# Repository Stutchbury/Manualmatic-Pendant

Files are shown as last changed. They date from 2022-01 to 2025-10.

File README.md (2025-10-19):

# The Manualmatic Pendant for LinuxCNC (or any other 4D system)

The Manualmatic Pendant enables you to perform the majority of routine LinuxCNC setup, manual and automatic operations without having to step away to a PC monitor.

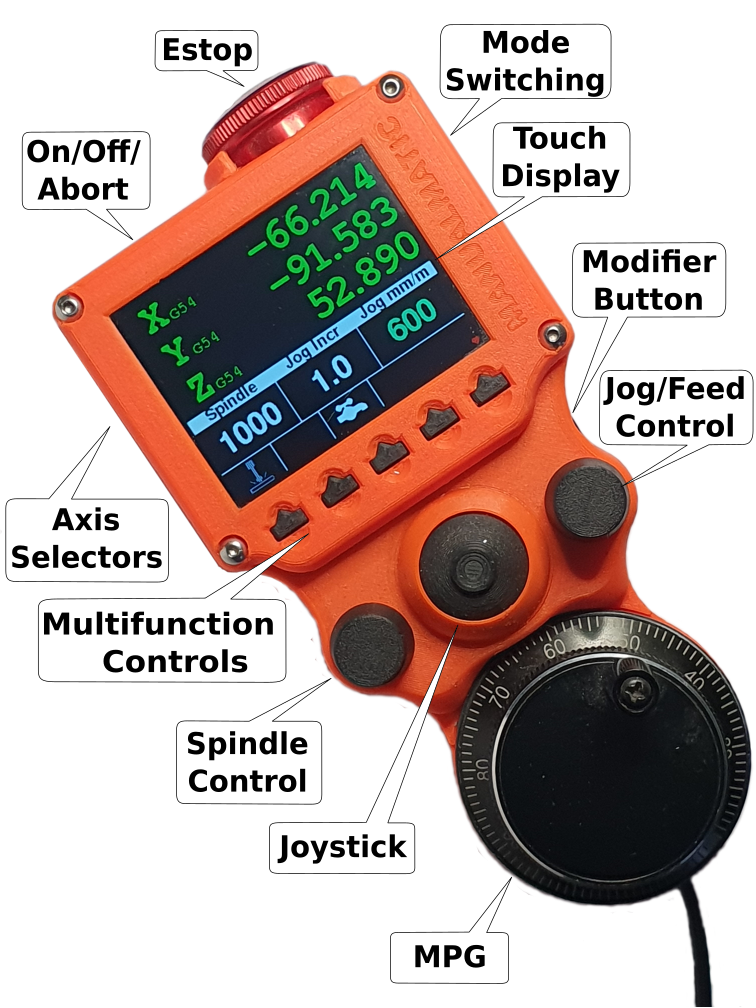
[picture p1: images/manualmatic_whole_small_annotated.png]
Manualmatic Controls Overview


Kicked off [here](https://forum.linuxcnc.org/18-computer/44682-arduino-teensy-python-interface-manualmatic-mpg-pendant) on the LinuxCNC forum and there's my place on [Discord](https://discord.gg/GDcEcWPKKm) for questions or discussion (PMs OK).

> User Guide **See the [User Guide](docs/USER_GUIDE.md) for the many features and functionality provided by the Manualmatic Pendant**

The currently released code implements almost all the functionality for both manual and auto control but don't take my word for it, here's a comment from das_machinist on [Discord](https://discord.gg/GDcEcWPKKm):

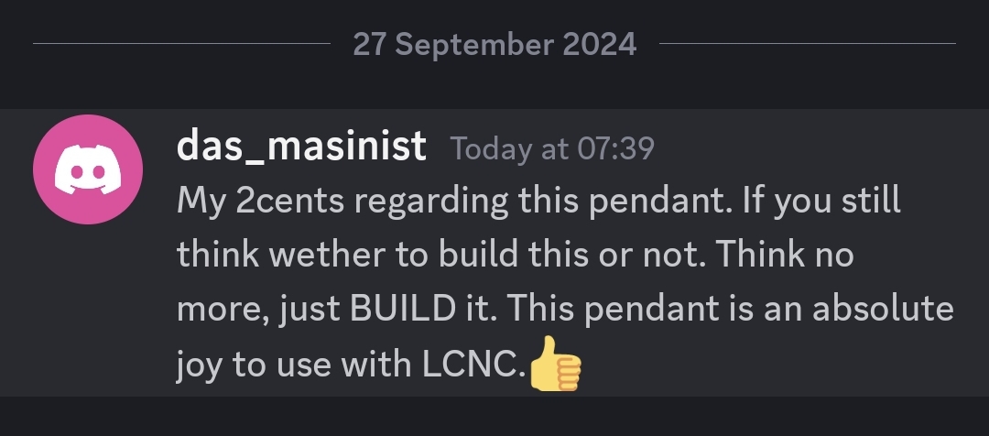
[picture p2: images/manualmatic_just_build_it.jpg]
Manualmatic Just Build It


Auto mode screen (uses the [DisplayUtils](https://github.com/Stutchbury/DisplayUtils) library):
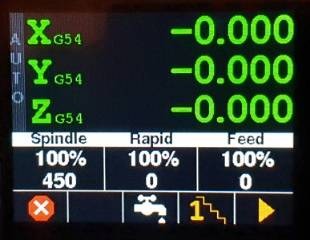
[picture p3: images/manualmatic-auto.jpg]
auto screen


Setting offsets (uses the [TouckKeypad](https://github.com/Stutchbury/TouchKeypad) library):
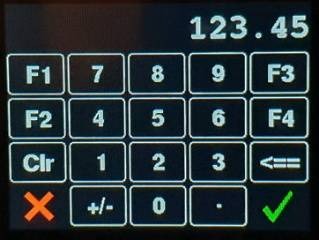
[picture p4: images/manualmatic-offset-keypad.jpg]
offset screen


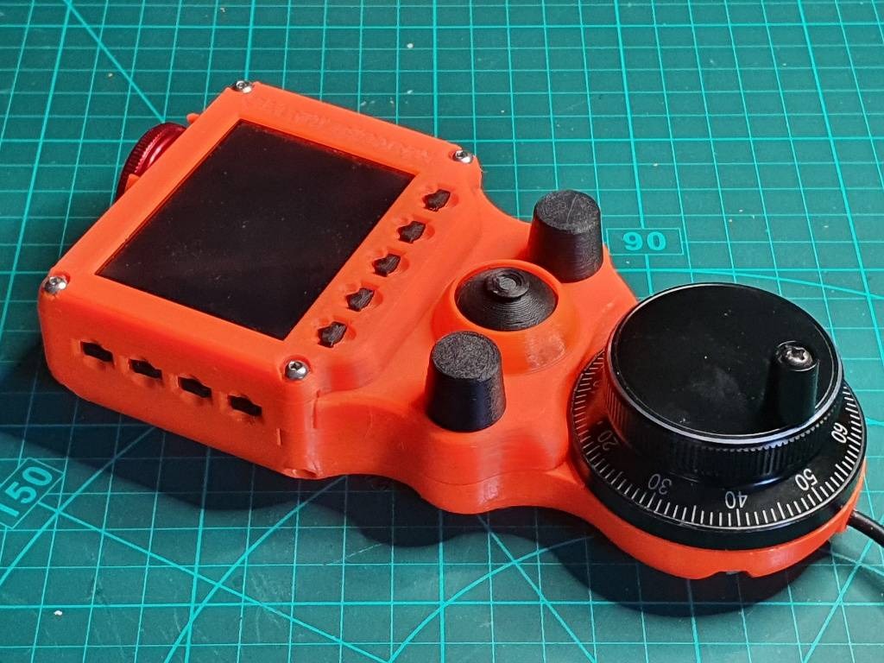
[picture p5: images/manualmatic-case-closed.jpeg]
manualmatic case
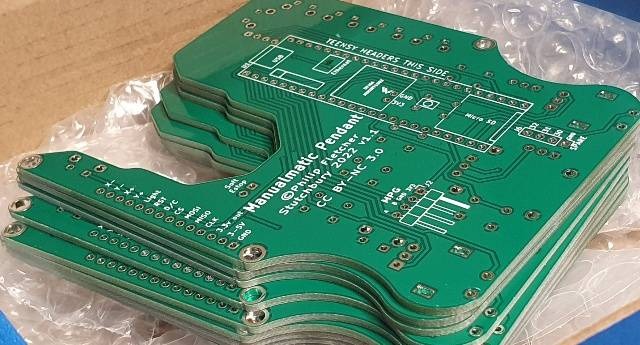
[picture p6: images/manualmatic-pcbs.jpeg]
manualmatic PCBs
There is now a complete 3D printable case  and a PCB  - contact me for details (email in my bio).

The pendant software has now been migrated to PlatformIO - using [Teensyduino](https://www.pjrc.com/teensy/td_download.html) via the Arduino IDE did end up too knarly.

Communication beween the [Teensy 4.1](https://www.pjrc.com/store/teensy41.html) and the [LinuxCNC Python Interface](https://www.linuxcnc.org/docs/html/config/python-interface.html) is over USB using a very simple protocol.

While the pendant prioritises working with LinuxCNC, in principle it is a fairly agnostic UI to control anything that you'd like to move in 4D that can read from & write to the serial port over USB.

## Getting Started

This was always intended to be "Almost Plug'n'Play"&trade; but does require the PlatformIO to upload to the Teensy and two files copied to your LinuxCNC config directory.

- Clone or download this repository and extract somewhere convenient (not usually on your LinuxCNC machine).

### PlatformIO Install

- Follow the install instructions here: https://platformio.org/platformio-ide

- Required libraries will be automatically downloaded based on the ```platformio.ini``` file.

- There are two folders of interest: 
  - The main codebase for the pendant: ```Software/PlatformIO/pendant/ManualmaticPendant``` or
  - A wiring check 'sketch': ```Software/PlatformIO/pendant/ManualmaticWiringCheck```

Open either of these folders and PlatformIO will allow you to compile and upload.

### LinuxCNC Install

- Copy both ```Manualmatic.py``` (the class def) and ```manualmatic``` (the component, lowercase, no file extension) to your LinuxCNC config directory.
- Add the following line to custom.hal (replace ```gmoccapy.ini``` with your ini file name):    
```loadusr -W ./manualmatic gmoccapy.ini```
- Change the ```manualmatic``` file to executable. e.g. ```chmod +x manualmatic``` 
- Plug your manualmatic pendant into a USB port - make sure appears as ```/dev/ttyACM0```
- Start LinuxCNC, preferably from the command line (to see any errors).

Note: LinuxCNC >= v2.9 now uses python3 with no default to 'python', so the ```manualmatic``` component file and the ```mock_cnc_machine.py``` file have been updated to use python3.

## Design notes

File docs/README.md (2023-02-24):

# Documentation

This folder will contain various documents relating to the build and use of the Manualmatic pendant.

The PCB:
- [Bill of Materials](BOM.md)
- [Soldering order of operations](SOLDERING.md)

3D Printable Case:
- [Printing the Case](../Hardware/case/v1.1/README.md)

Software
- [LinuxCNC Install](LINUXCNC_INSTALL.md)

User Guide
- [This](pendant_user_guide.pdf) is currently more an early development aid rather than a user guide as it describes the functions of each control on the Manualmatic rather than describing how to perform tasks. Rewrite is required...

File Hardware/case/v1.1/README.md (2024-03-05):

# Manualmatic Pendant Case v1.1

Designed around the v1.1 PCB to be 3D printed. Tolerances are built in but you may need to tune your slicer settings to get an accurate fit.

## Base
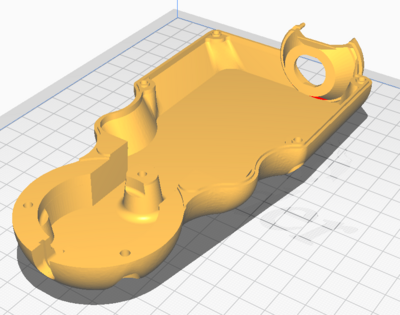
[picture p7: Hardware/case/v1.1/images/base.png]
base


Print 'as is' - will require supports for the MPG and display holes. I also used support for the e-stop shroud but this may not be essential.

## Encoder Panel
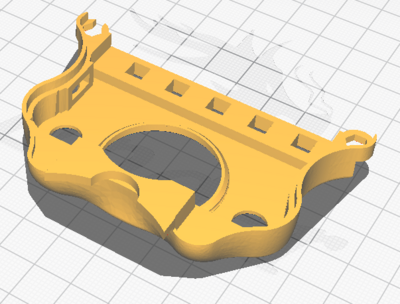
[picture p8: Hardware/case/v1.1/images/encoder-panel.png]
encoder panel


Flip this over to print. Will require supports for the display holes/lugs and the lip that will end up under the MPG. I also generated support for the modifier button hole.

## Left/Right Side Button Panels
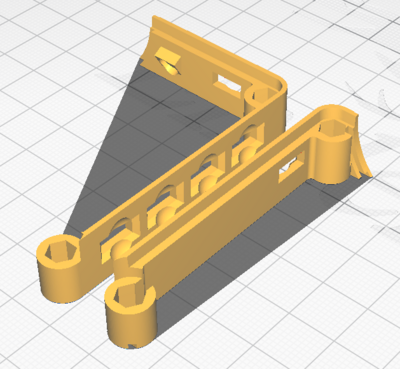
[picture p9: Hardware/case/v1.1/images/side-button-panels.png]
left/right side button panels


Flip over to print - bed adhesion is critical as these have a tendency to warp with PETG, so print in the centre of the bed and, if possible, with an enclosure.
Support is not necessarily required but I generated it for the button holes.
Ensure the top grooves are clear before assembly (test fit with the display bezel).

## Display Bezel
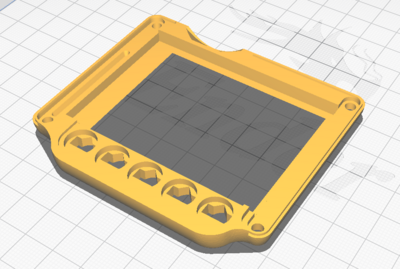
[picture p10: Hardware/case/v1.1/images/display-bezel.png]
display bezel


Flip over to print. Support is required only for the corner hole counterbores. 

## Cable Wedge x2

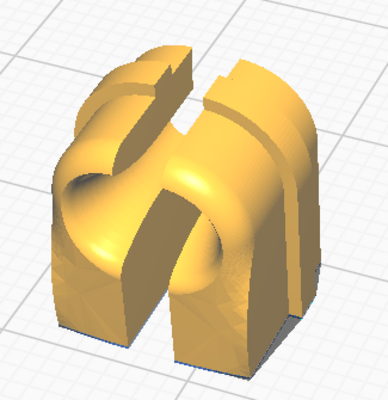
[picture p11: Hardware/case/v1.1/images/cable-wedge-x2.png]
cable wedge


Mirror one part and print both standing on the (only) flat face. Support is advised for the hole.

These should slide fairly easily into the base (ie, don't spring the gap open or you won't get the MPG studs in). Before putting it all together, make sure your cable fits through the hole with the two faces just about touching - to adjust, fit the parts in the base and ream out with a drill bit or needle file.

## Joystick Dome
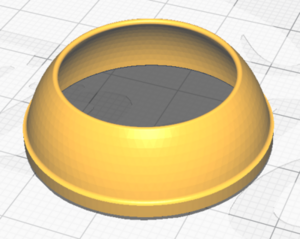
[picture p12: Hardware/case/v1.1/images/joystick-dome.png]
joystick dome


Print 'as is'. Does not require support. Push fit into the top of the encoder panel.

## Joystick Button
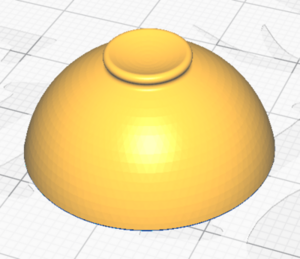
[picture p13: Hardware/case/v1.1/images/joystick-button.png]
joystick button


Print 'as is' - requires support but remove very carefully!

Currently this is an 'inside' button - may redesign as an 'outside' button (ie dome underneath).

## Side Buttons x7
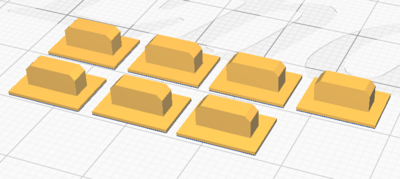
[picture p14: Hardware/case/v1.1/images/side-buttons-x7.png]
side buttons


Print as is. These can be taped to the case (inside) before assembly but don't overlap the rebate.

## Row Buttons x5
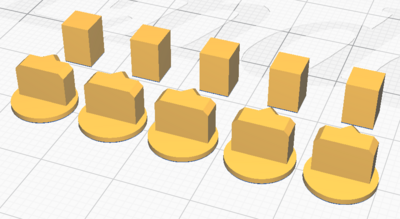
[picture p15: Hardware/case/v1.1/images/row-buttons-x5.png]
row buttons


Print as is - each button is in two parts. The top part can be taped into the display bezel before assembly (there's a little relief for the tape).

## Encoder Knobs x2

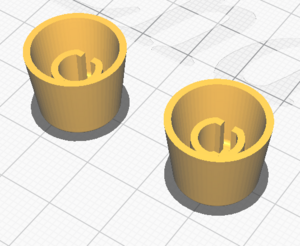
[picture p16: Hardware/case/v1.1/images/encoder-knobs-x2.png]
encoder knobs


Print as is, no support required.

## MPG Spanner

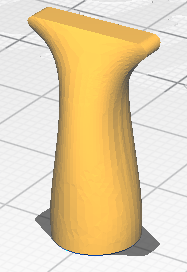
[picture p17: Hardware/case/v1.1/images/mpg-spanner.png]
mpg spanner


Print 'as is', I do not advise using support. 

Use this to hold & tighten the nuts for the MPG.

## Cradle

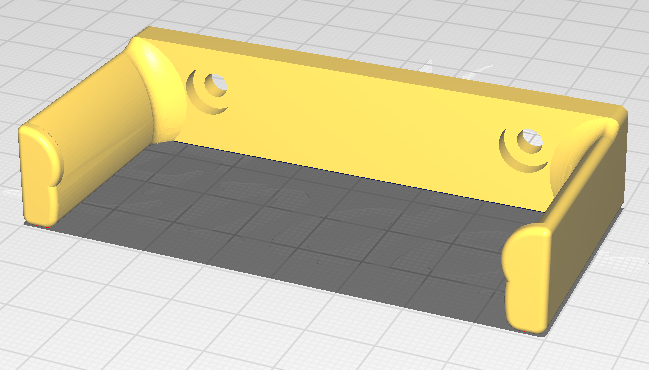
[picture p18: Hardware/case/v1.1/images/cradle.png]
cradle


Print 'as is', no support required.

I used 5 walls to ensure line continuity from fixing holes to support legs.

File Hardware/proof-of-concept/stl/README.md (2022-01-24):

# Proof of concept 3D prints

This is a 'cradle' and 'bridge'to hold the Teensy 4.1, touch screen, buttons and rotary encoders/MPG.

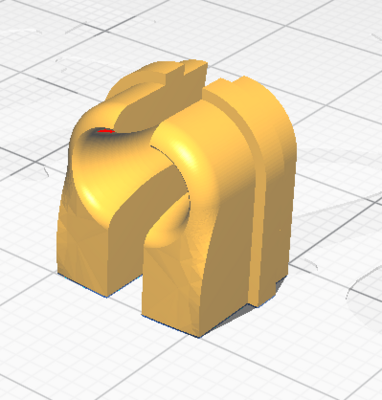
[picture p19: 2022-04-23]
Hardware/case/v1.1/images/cable-wedge.png

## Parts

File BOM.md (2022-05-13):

# Bill of Materials

These are the components I have chosen to use for the Manualmatic when using the PCB.

| Item | Ref	| Qty	| Value | Datasheet |  Manufacturer |
| ---- | ---- | --- | ----- | --- | --- |
|MPG  | U1 |	1	| Teensy4.1| https://www.pjrc.com/store/teensy41.html | Teensy |
|MPG | J1 |	1	| Adafruit-1770-2.8-TFT-Touch	 |	https://www.adafruit.com/product/1770	| Adafruit |
|MPG  | S12 S13 | 2	| PEC11R-4115F-S0018	|	https://www.mouser.co.uk/datasheet/2/54/PEC11R-777457.pdf	| Bourns |
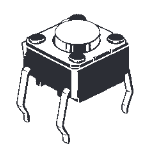
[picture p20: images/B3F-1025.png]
| | S1 S2 S3 S4 S5 |	5	| B3F-1025 |	https://www.mouser.co.uk/datasheet/2/307/en-b3f-13826.pdf	| Omron |
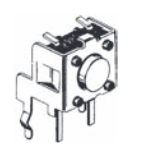
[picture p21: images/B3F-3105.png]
| | S6 S7 S8 S9 S10 S11 S14 | 7	| B3F-3105| https://www.mouser.co.uk/datasheet/2/307/en-b3f-13826.pdf |		Omron |
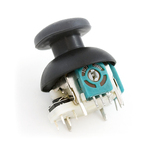
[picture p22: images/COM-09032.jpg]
|  | U2 |	1	|COM-09032	| https://www.sparkfun.com/products/9032	| SparkFun Electronics |
|MPG | J2 | 1 | Right angle male header for MPG| | Generic|

Unless you're brave enough to solder both the Teensy and the Adafruit display to the PCB (I'm not and the case *is not* designed for direct soldering), you'll need 48 female headers for the Teensy and 14 female headers for the display.

I bought these as 4 x 12 pins and 2 x 7 pins as this was significantly cheaper than contiguous blocks. You may need to lightly file adjacent edges so they don't bow the board when soldered in.

You'll also need a 60mm Manual Pulse Generator (ebay ones seem to work just fine, unlike the two encoder buttons), a 16mm Estop button and a tight/compact right angle micro-USB cable (2-3m) - preferably in the orientation shown below.

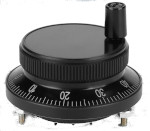
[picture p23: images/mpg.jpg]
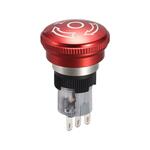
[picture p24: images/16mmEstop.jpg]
estop
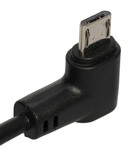
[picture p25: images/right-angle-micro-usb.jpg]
micro USB
   

J3 (2 pin, soft estop), J3, J4 & J5 (3 & 4 pin spare breakouts) are optional right angle male headers.

**Notes:**

1. I recommend sourcing the two encoder buttons from a known supplier unless you are sure of their provenance - I have had two 'ebay specials' fail which have effectively wasted the PCBs. The specified encoders also have a short shaft to work with the case.
2. The 5 push buttons and 7 right angle buttons are of a specific detent force (orange button) and closely match the detent force of the two encoders and the joystick, maximising the consistency of 'feel'. Ebay ones are of very variable detent strength - often very low.
3. The joystick PCB footprint will only fit the Sparkfun Deluxe COM-09032 joystick. The Xbox replacements have a different footprint (and the ebay ones have 'interesting' resistance characteristics).
4. If you are using the 3D printed case (recomended, it's a work of art ;-)), you'll need 4 x 11mm brass stand-offs and 8 x 8-10mm M3 dome/button head screws.
5. We are using the Adafruit display in SPI mode, so you will need to bridge the pads on the back of the board as per: https://learn.adafruit.com/adafruit-2-8-and-3-2-color-tft-touchscreen-breakout-v2/spi-wiring-and-test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

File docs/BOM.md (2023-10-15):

# Bill of Materials

These are the components I have chosen to use for the Manualmatic when using the PCB.

|Num| Item | Ref	| Qty	| Value | Datasheet/Notes |  Manufacturer |
|--| ---- | ---- | --- | ----- | --- | --- |
|1|Teensy 4.1  | U1 |	1	| Teensy4.1| https://www.pjrc.com/store/teensy41.html | Teensy |
|2|Adafruit Display | J1 |	1	| Adafruit-1770-2.8-TFT-Touch	 |	https://www.adafruit.com/product/1770	| Adafruit |
|3|Encoder button  | S12 S13 | 2	| PEC11R-4115F-S0018	|	https://www.mouser.co.uk/datasheet/2/54/PEC11R-777457.pdf	| Bourns |
|4|push button | S1 S2 S3 S4 S5 |	5	| B3F-1025 |	https://www.mouser.co.uk/datasheet/2/307/en-b3f-13826.pdf	| Omron |
|5|right angle push button | S6 S7 S8 S9 S10 S11 S14 | 7	| B3F-3105| https://www.mouser.co.uk/datasheet/2/307/en-b3f-13826.pdf |		Omron |
|6|Joystick  | U2 |	1	|COM-09032	| https://www.sparkfun.com/products/9032	| SparkFun Electronics |
|7|MPG right angle header | J2 | 1 | 4 pin right angle male header| For MPG | Generic|
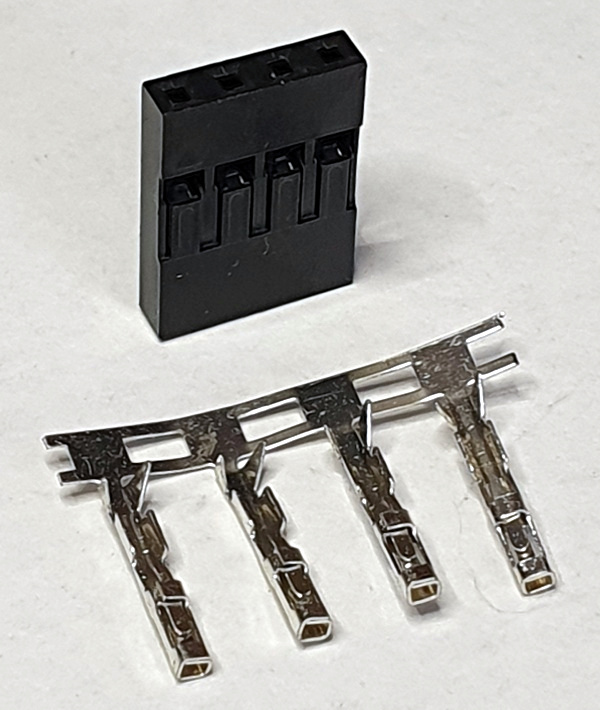
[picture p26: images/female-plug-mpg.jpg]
MPG female plug
|8| | n/a  | 1 | 4 pin female plug| For MPG | Generic|
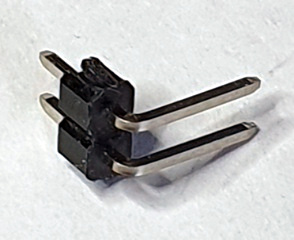
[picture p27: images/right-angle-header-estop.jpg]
Estop right angle header
|9| | J3 | 1 | 2 pin right angle male header | For Estop button | Generic|
|10|Estop female plug | n/a  | 1 | 2 pin female plug| For Estop button | Generic|
|11|Teensy female headers | U1 | 4 x 12pin | Female headers | To plug Teensy into PCB. <br/>8.5mm high, excluding pins | Generic|
|12|Display female headers | J1 | 2 x 7pin| Female headers | To plug in display into PCB. <br/> 8.5mm high, excluding pins | Generic|
|13|MPG | n/a | 1 | 60mm Manual Pulse Generator | ebay ones seem to work just fine, unlike the encoder buttons. Some may have 6 connections but you can ignore A- & B-.| Generic|
|14|Estop | n/a | 1 | 16mm Estop button | Example: https://www.ebay.co.uk/itm/184899597984 | Generic|
|15|USB Cable | n/a | 1| 2-3m tight/compact right angle micro-USB cable | Example: https://www.ebay.co.uk/itm/194756552182?var=494734226747 | Generic|
|16|PCB | n/a | 1 | Custom PCB| Contact me (email address on my profile)  | Stutchbury|
|17|Stand-offs | n/a | 4 | 11mm stand-offs & screws| | Generic |

Unless you're brave enough to solder both the Teensy and the Adafruit display to the PCB (I'm not and the case *is not* designed for direct soldering), you'll need 48 female headers for the Teensy (item 11) and 14 female headers for the display (item 12).

I bought these as 4 x 12 pins and 2 x 7 pins as this was significantly cheaper than contiguous blocks. You may need to lightly file adjacent edges so they don't bow the board when soldered in.

Items 7-10 above can be omitted if you solder the MPG & Estop wires directly to the PCB.

J4 & J5 (3 & 4 pin spare breakouts) are optional right angle male headers.

**Notes:**

1. I recommend sourcing the two encoder buttons from a known supplier unless you are sure of their provenance - I have had two 'ebay specials' fail which have effectively wasted the PCBs. The specified encoders also have a short shaft to work with the case.
2. The 5 push buttons and 7 right angle buttons are of a specific detent force (orange button) and closely match the detent force of the two encoders and the joystick, maximising the consistency of 'feel'. Ebay ones are of very variable detent strength - often very low.
3. The joystick PCB footprint will only fit the Sparkfun Deluxe COM-09032 joystick. The Xbox replacements have a different footprint (and the ebay ones have 'interesting' resistance characteristics).
4. If you are using the 3D printed case (recomended, it's a work of art ;-)), you'll need 4 x 11mm brass stand-offs and 8 x 8-10mm M3 dome/button head screws.
5. We are using the Adafruit display in SPI mode, so you will need to bridge the pads on the back of the board as per: https://learn.adafruit.com/adafruit-2-8-and-3-2-color-tft-touchscreen-breakout-v2/spi-wiring-and-test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

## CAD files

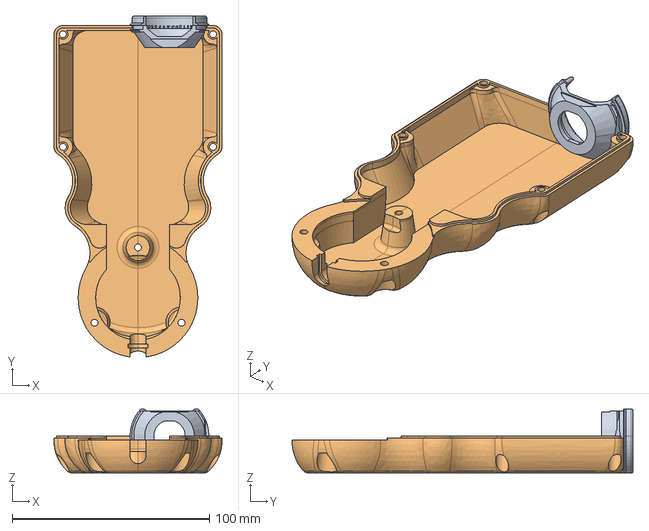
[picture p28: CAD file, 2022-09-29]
Hardware/case/v1.1/step/base-Part.step
85.3 x 173.0 x 32.3 mm

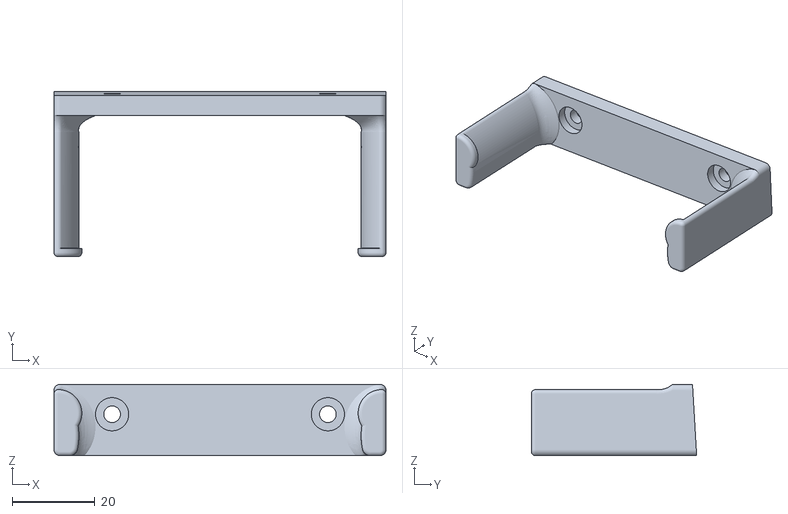
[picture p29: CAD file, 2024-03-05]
Hardware/case/v1.1/stl/cradle.stl
80.0 x 39.8 x 17.2

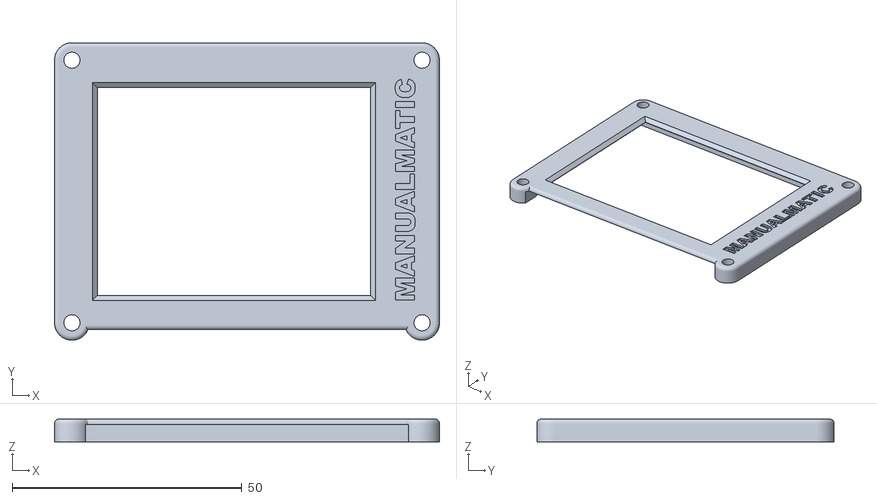
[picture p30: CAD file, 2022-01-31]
Hardware/proof-of-concept/stl/bezel-Part.stl
83.8 x 64.7 x 5.00

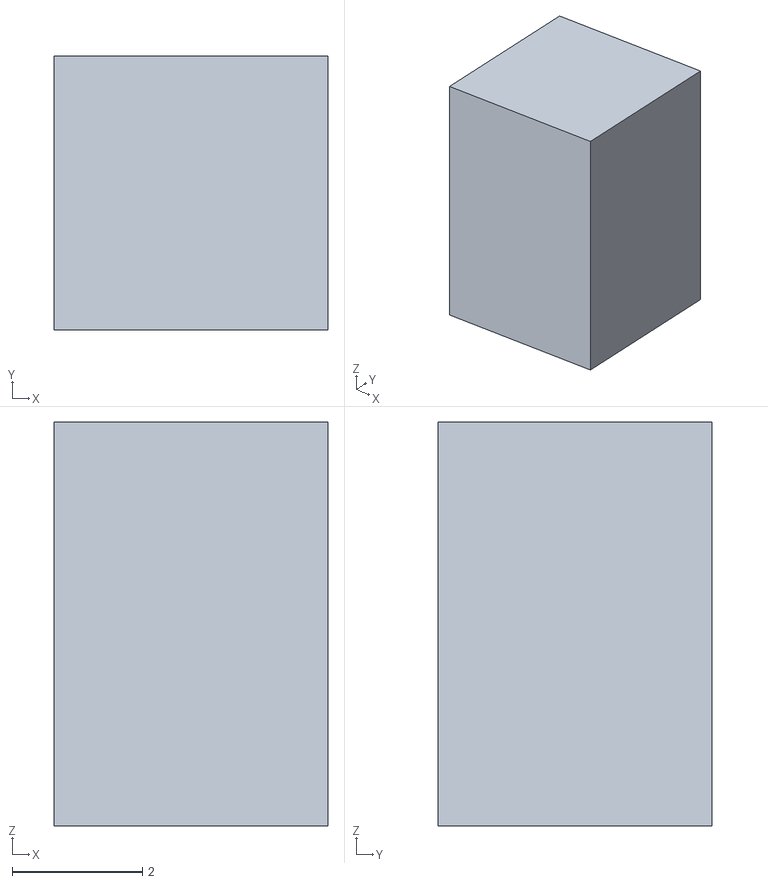
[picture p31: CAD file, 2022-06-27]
Hardware/case/v1.1/stl/row-button-cube.stl
4.20 x 4.20 x 6.20

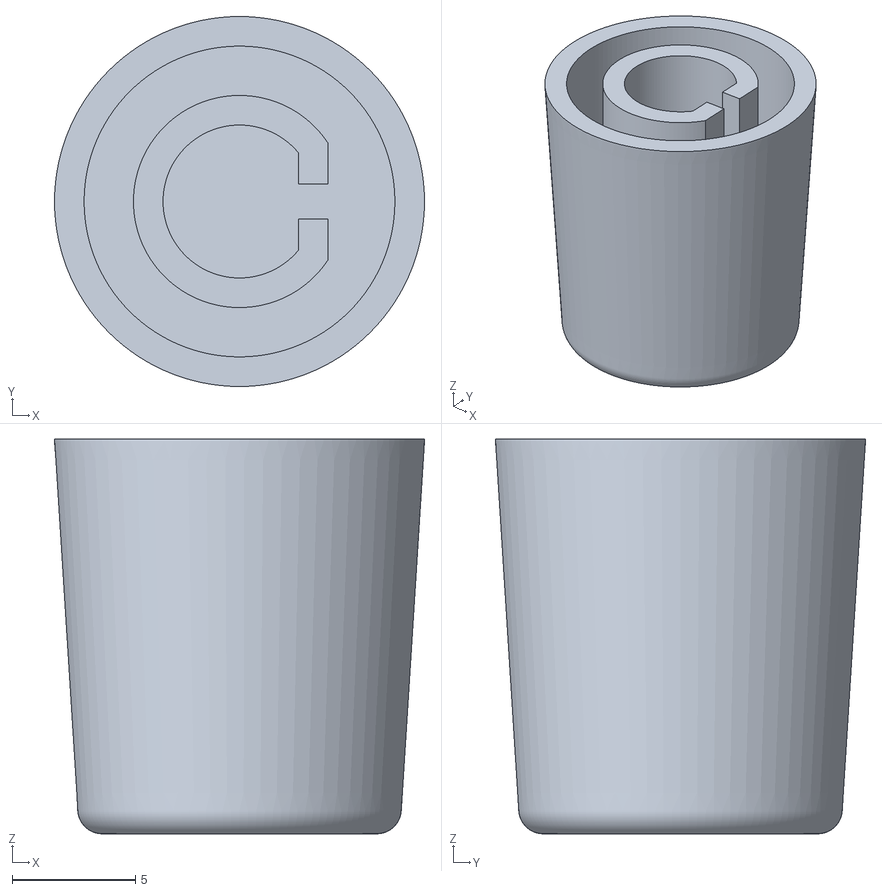
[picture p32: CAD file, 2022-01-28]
Hardware/proof-of-concept/stl/knob-PartBody16mm.stl
15.0 x 15.0 x 16.0

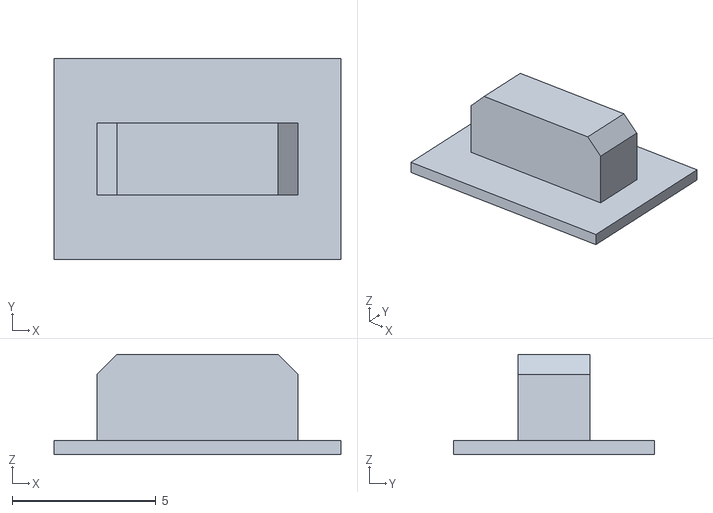
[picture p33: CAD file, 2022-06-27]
Hardware/case/v1.1/stl/side-button.stl
10.0 x 7.00 x 3.50

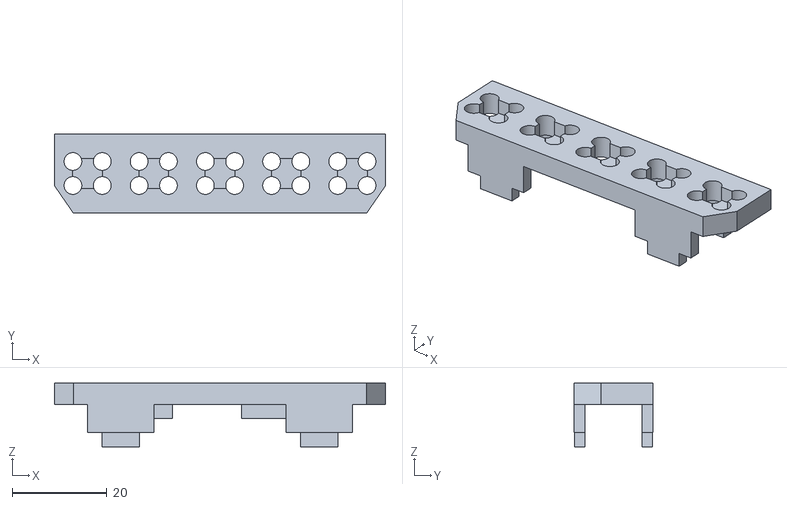
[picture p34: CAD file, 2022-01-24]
Hardware/proof-of-concept/stl/pendant-test2-PartBody_keypad1.stl
70.0 x 16.8 x 13.5

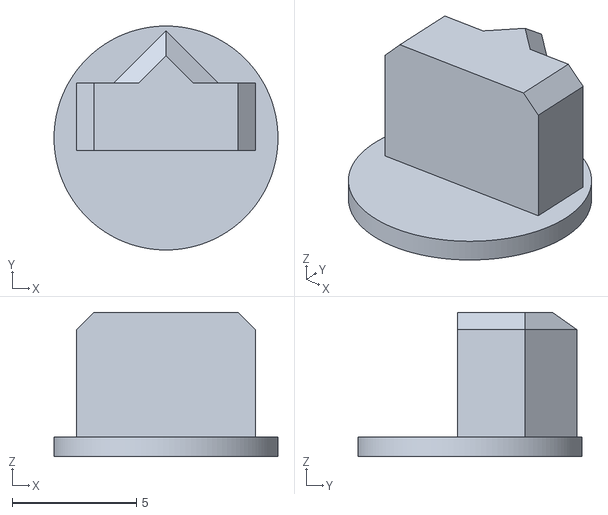
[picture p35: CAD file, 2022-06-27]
Hardware/case/v1.1/stl/row-button.stl
9.00 x 9.00 x 5.80

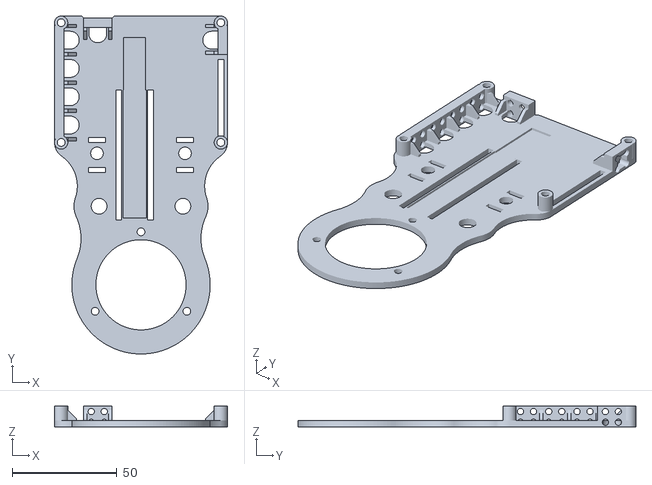
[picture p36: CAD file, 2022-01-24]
Hardware/proof-of-concept/stl/pendant-test2-PartBody_base.stl
82.5 x 161.2 x 10.0

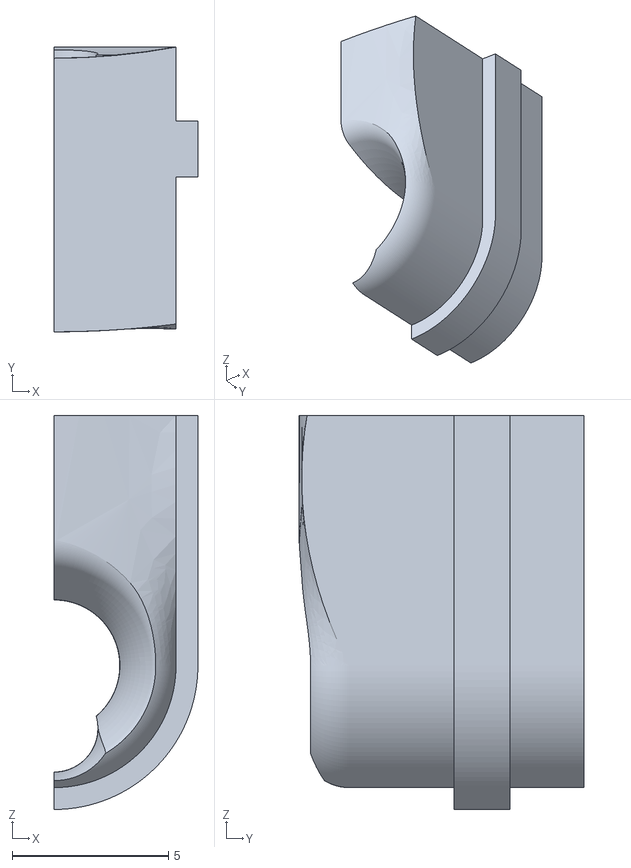
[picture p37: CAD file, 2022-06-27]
Hardware/case/v1.1/stl/cable-grip-2-wire.stl
4.60 x 9.11 x 12.6

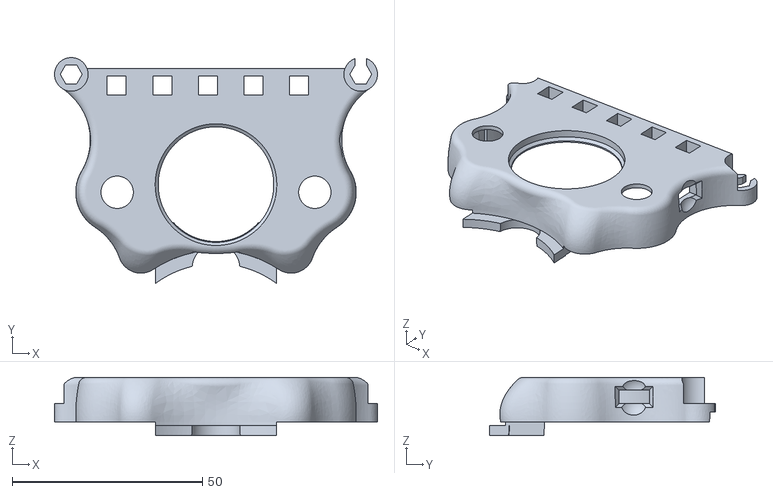
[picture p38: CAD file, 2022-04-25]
Hardware/case/v1.1/stl/encoder-panel.stl
85.0 x 59.4 x 15.3

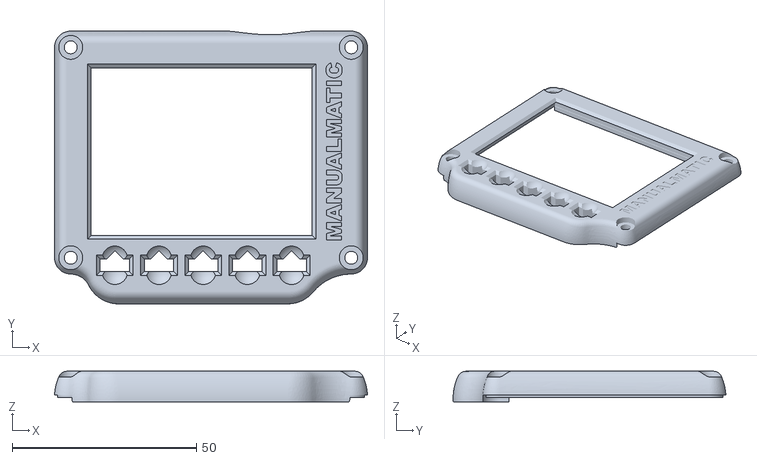
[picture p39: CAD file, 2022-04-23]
Hardware/case/v1.1/stl/display-bezel.stl
85.0 x 74.1 x 8.30

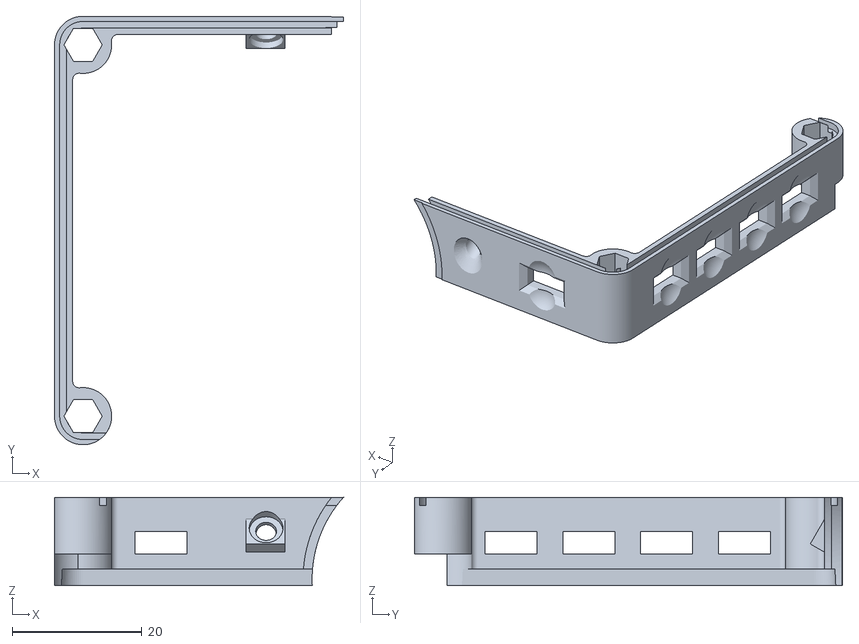
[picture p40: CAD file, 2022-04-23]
Hardware/case/v1.1/stl/button-panel-left.stl
44.5 x 65.9 x 13.6

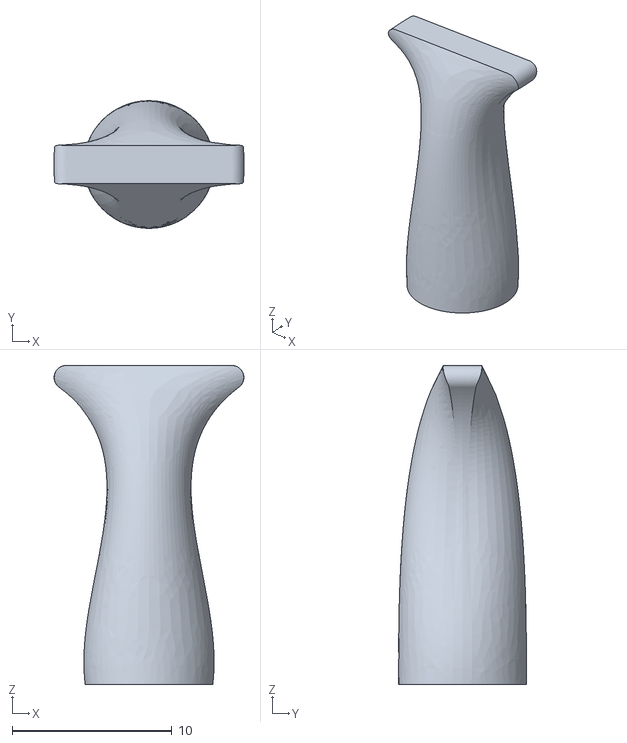
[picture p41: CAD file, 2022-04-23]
Hardware/case/v1.1/stl/mpg-spanner-5.5mm.stl
11.9 x 8.01 x 20.0

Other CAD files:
Hardware/case/v1.1/stl/joystick-knob.stl
Hardware/case/v1.1/stl/encoder-knob.stl
Hardware/case/v1.1/stl/button-panel-right.stl
Hardware/case/v1.1/stl/cable-wedge.stl
Hardware/case/v1.1/stl/joystick-dome.stl

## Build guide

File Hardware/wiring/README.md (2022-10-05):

# Manualmatic Pendant Schematic

[This](manulmatic-schematic.pdf) is how I have wired the [Teensy 4.1](https://www.pjrc.com/store/teensy41.html), the [Adafruit 2.8" Touch screen](https://learn.adafruit.com/adafruit-2-8-and-3-2-color-tft-touchscreen-breakout-v2) and the various encoders & buttons for the proof of concept. The code base is written to this schematic.

# PCBs and Components

There is now a PCB for this project which is somewhat easier than the molex birds nest shown below - the case is also designed around the board. BoM details are [here](../../docs/BOM.md) and information/pictures for soldering to the PCB is [here](../../docs/SOLDERING.md).

I have a few spare PCBs and small stock of the board mounted components (thanks to minimum order levels). Please contact me via email (in my bio) if you are interested.

# Proof of Concept (*not* recommended!)

The picture below shows the wiring of the proof-of-concept. While this worked and was fairly robust, it's not an approach I can recommend! It is also prior to adding the joystick.

**Out of Date***

Where possible I have grouped pins together, so if you have access to a Molex crimper the wiring is not too onerous. I strongly suggest making short 'ribbon cables' to keep the birds nest tidy(ish).

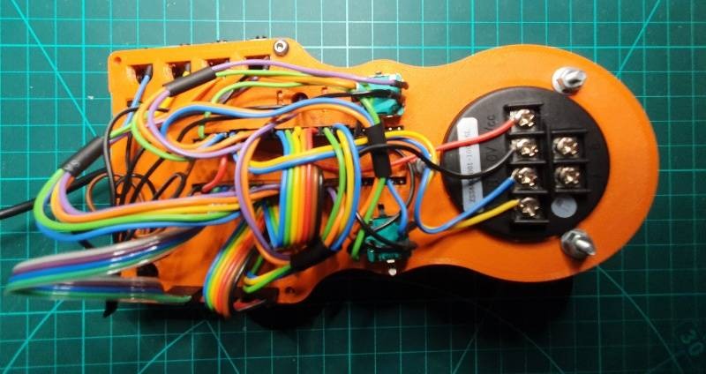
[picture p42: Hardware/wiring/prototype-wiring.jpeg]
pendant wiring


The 'bridge' for the configurable button row holds the Teeensy in place at the centre but probably better to push all the Molexes onto the Teensy pins before attaching the display.

The wiring check has now moved to 'Software': [ManualmaticWiringCheck](https://github.com/Stutchbury/Manualmatic-Pendant/tree/main/Software/PlatformIO/pendant/ManualmaticWiringCheck)  

This is a PlatformIO 'sketch' that will enable you to check everything is wired as expected, including the display and touchscreen.

The schematic is [here](manulmatic-schematic.pdf).

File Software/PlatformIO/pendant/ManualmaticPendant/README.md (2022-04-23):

# Manualmatic Pendant PlatformIO Code

This is the PlatformIO port of the Arduono codebase for the Manualmatic Pendant. Still lots of features to be added but all the primary functions are implemented. There will probably be structural changes as we're not no loger constrained by the Arduino IDE.

See User Guide for a full description of implemented functionality.

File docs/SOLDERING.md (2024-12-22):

# Soldering the PCB

A few notes on soldering the components to the PCB - primarily the order of operations that has worked best for me.

The Teensy 4.1 and the Adafruit 2.8" Touchscreen are plugged in to female headers on the PCB - all other components are soldered directly to the board.

### Order of Operations

Ensure all components are fully seated and square to the PCB. The 3D printed case has some tolerance built in but not a lot.

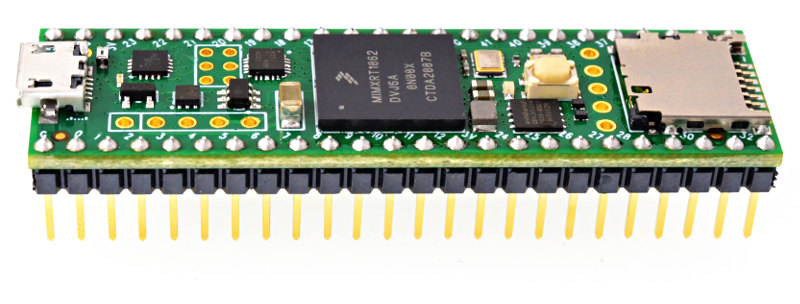
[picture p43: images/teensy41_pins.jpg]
Teensy Male Headers
1. **Teensy Male Headers**: Solder the male headers to the back of Teensy 4.1 (ie pins are on the opposite side to the USB and SD card) on both edges.   <br/>   
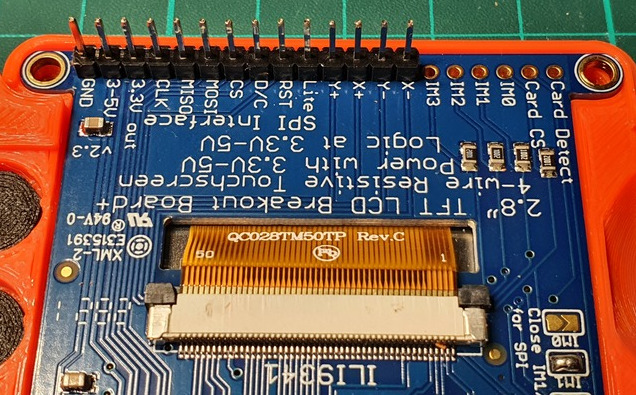
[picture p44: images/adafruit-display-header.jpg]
2. **Display Male Header**: Solder ***just 14*** male header pins to the Adafruit display. I recommend temporarily fitting the 11mm brass standoffs to attach the display to the PCB to ensure everything aligns. *Do not solder the female headers to the PCB yet*.  <br/>    **NOTE**: The IM1, IM2 and IM3 SPI Mode Jumpers (on the back of the display) must be closed with solder as per the Adafruit instructions here: https://learn.adafruit.com/adafruit-2-8-and-3-2-color-tft-touchscreen-breakout-v2/spi-wiring-and-test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  (You can see IM1 in the photo below)  <br/>     
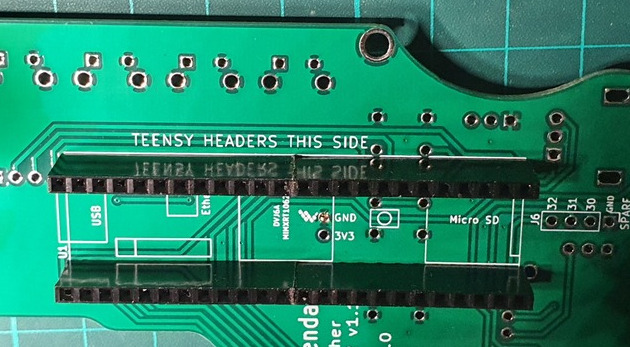
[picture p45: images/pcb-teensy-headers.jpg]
Teensy Female Headers
3. **Teensy Female Headers**: Solder the two 24 pin female headers (reference U1) for the Teensy to the back of the PCB. If you are using 4 off 12 pin female headers (a much more economical option) you may need to lightly file adjacent ends to ensure the board is not bowed.   <br/>    
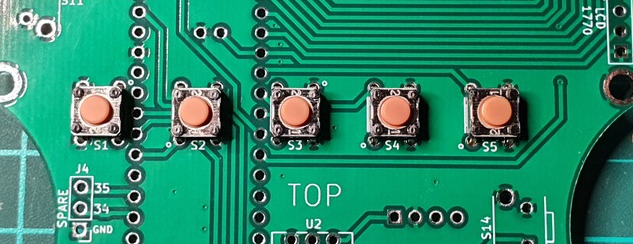
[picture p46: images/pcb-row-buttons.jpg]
Row Buttons
4. **Row Buttons**: Fit the five 'row buttons' (B3F-1025 in references S1, S2, S3, S4 & S5) to the top of the board and solder from the back.   <br/>    
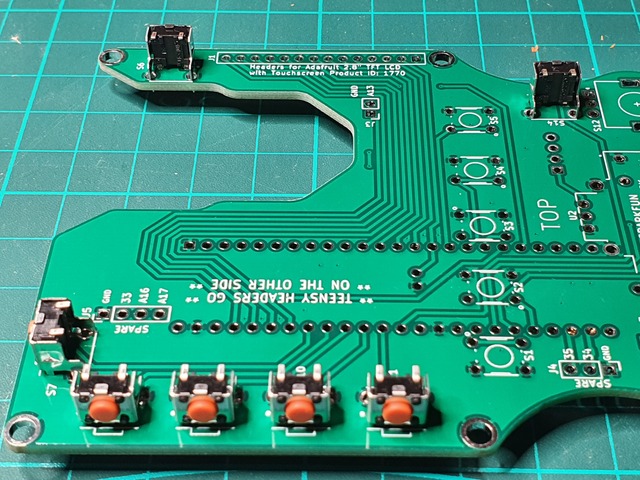
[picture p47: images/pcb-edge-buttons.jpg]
Edge Buttons
5. **Edge Buttons**: Fit all seven edge buttons (B3F-3105 in references S6, S7, S8, S9, S10, S11 & S14) and solder from the back. The board will rest on the tops of the buttons helping to ensure they go in square if you press down on the PCB while soldering.   <br/>  
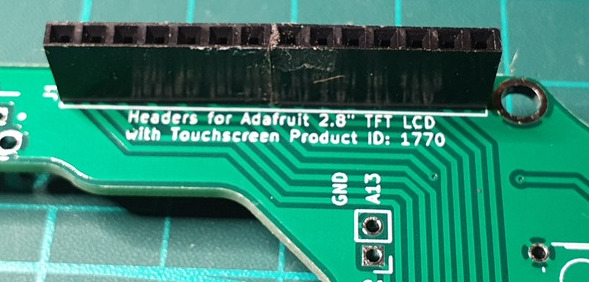
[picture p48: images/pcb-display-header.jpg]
Display Female Headers
6. **Display Female Header**:  Solder the female header for the display (reference J1) to the front of the board. I recommend temporarily fitting the 11mm brass standoffs to ensure everything aligns. (I probably should've cleaned up the filings that stuck to the tape residue before taking the photo...)  <br/>  
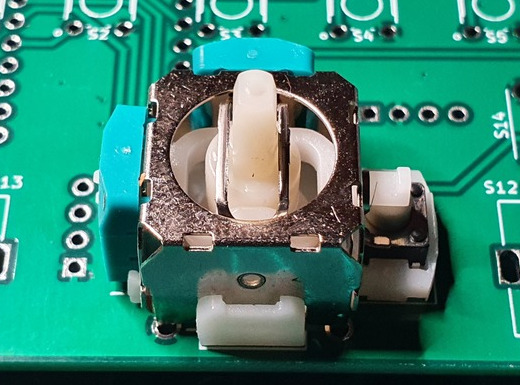
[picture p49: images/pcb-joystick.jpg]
Joystick
7. **Joystick**: Spend some time cursing as you try to align all the pins on the joystick (COM-09032 in reference U2). It can take a while. Press the button area of the joystick *very* firmly down as you solder those pins first and when soldering the other pins, ensure the rest of the base is tight (or at least parallel) to the PCB or the joystick will not be central when it is at rest.  <br/>   
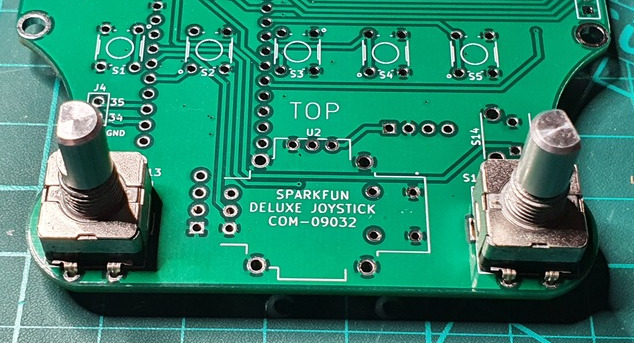
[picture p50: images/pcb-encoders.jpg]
Encoders
8. **Encoders**: Fit the two encoder buttons (PEC11R-4115F-S0018 in references S12 & S13). They *should* 'click' into place and hold themselves tight to the PCB while being soldered.   <br/>  
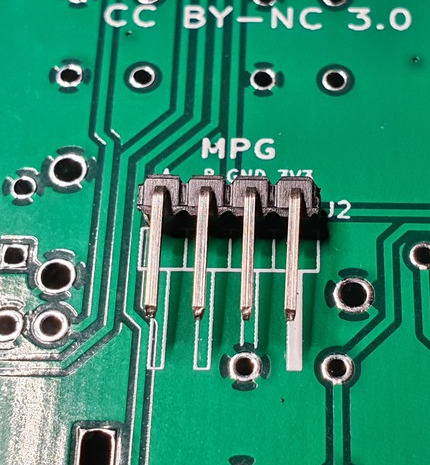
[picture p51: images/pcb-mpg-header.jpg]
9.  **MPG Header**: Solder the right angle male header for the MPG to the back of the board (reference J2). You can optionally solder the MPG wires directly to the PCB -  I'd recommend hot glue strain relief as there's a fair bit of fiddling when putting the case together.   <br/>     

10.  **Soft Estop**: These headers are for a soft estop - the switch must be normally closed (NC) as the estop is actived when the switch is open.
I highly recommend putting the headers on the top for ease of assembly. <br/> 
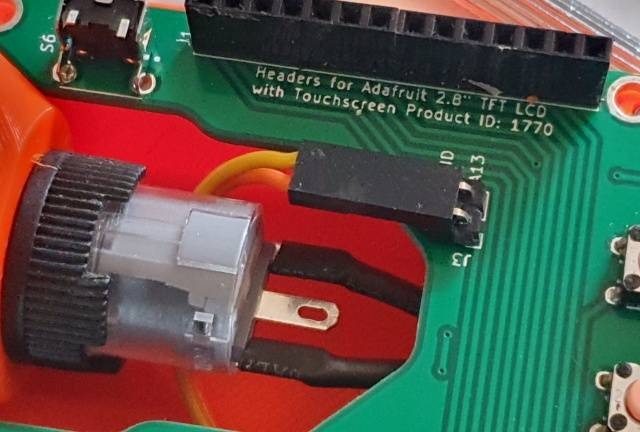
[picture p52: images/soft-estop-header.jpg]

  <br/>
If you are using a a hard wired (or no) estop, you can either bridge these headers or change `useSoftEstop` to `false` in `ManualmaticConfig.h` to free up J3 (GND & pin 27/A13) as spare connection.  <br/>
**NOTE:** Please see main documentation to check if you need to implement the LinuxCNC estop_latch. This is intended as a supplementary estop, not to re[lace a hard wired one.

### The Finished PCB

For reference here are the top & bottom views of the PCB (with the Teensy 4.1 plugged in):
<br/> 
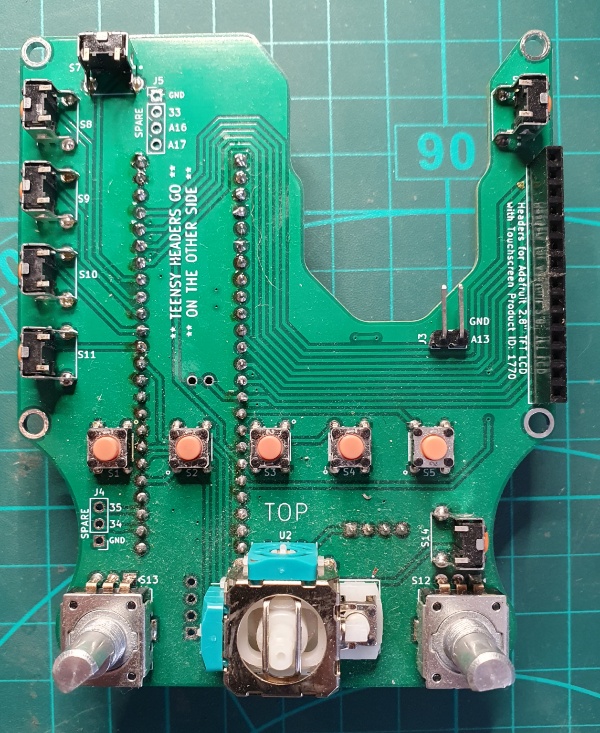
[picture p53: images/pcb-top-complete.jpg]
PCB top complete


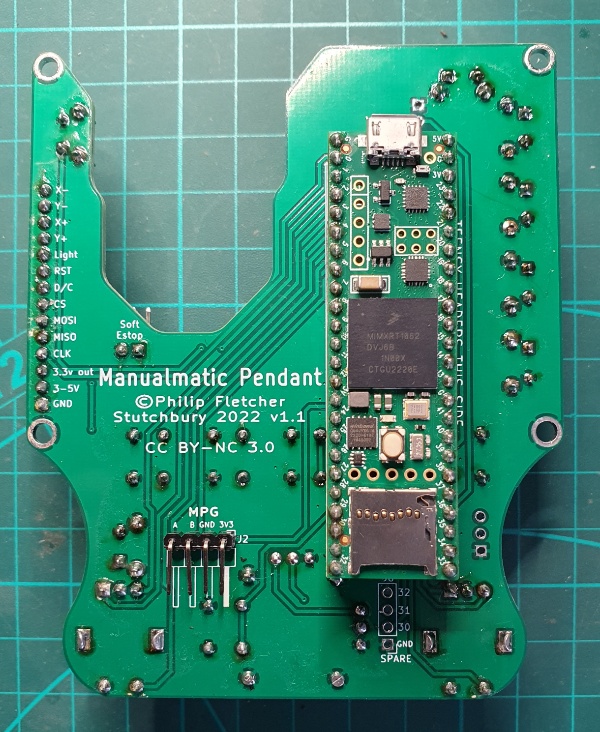
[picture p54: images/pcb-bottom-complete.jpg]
PCB bottom complete


### Optional Connections

There are three 'spare' sets of pin headers on the board that will all work with right angle headers. I would not solder these in unless you intend to use them.
1. **J5**: Provides GND, pins 33, A16 & A17. Headers intended to go on the top of the board and GND+33 are provisionally for a 3mm LED 'torch' built into the case.
2. **J4**: Provides GND, pins 34 (RX8) & 35 (TX8). Headers intended to be on top of the board.
3. **J6**: Provides GND, 30, 31 & 32. Headers intended to be on bottom of the board.

The 3V3 & GND in the middle of the Teensy headers is intended for a Teensy 4.0 (untested and the 5 physical 'row buttons' will not be connected) but can otherwise be used as a 3V3 supply.

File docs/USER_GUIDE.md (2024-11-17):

# Manualmatic User Guide <!-- omit from toc -->

- [Operations](#operations)
  - [Controls Overview](#controls-overview)
  - [Display Overview](#display-overview)
  - [Machine On/Off, Abort Operation and Estop](#machine-onoff-abort-operation-and-estop)
    - [Turning On](#turning-on)
    - [Turning Off](#turning-off)
    - [Abort Operation](#abort-operation)
    - [Soft Estop](#soft-estop)
  - [Operating Modes (Manual, MDI, Auto)](#operating-modes-manual-mdi-auto)
    - [Changing Modes](#changing-modes)
  - [Manual Mode](#manual-mode)
    - [Controlling Jog/Feed Speeds \& Increment](#controlling-jogfeed-speeds--increment)
      - [Changing the Jog/Feed Speed](#changing-the-jogfeed-speed)
      - [Changing Jog Increments](#changing-jog-increments)
      - [Switching between Tortoise \& Rabbit Range](#switching-between-tortoise--rabbit-range)
      - [Resetting Jog Speeds to Defaults](#resetting-jog-speeds-to-defaults)
    - [Moving the Axis (Jogging)](#moving-the-axis-jogging)
      - [Using the MPG](#using-the-mpg)
      - [Using the Joystick](#using-the-joystick)
      - [Power Feed](#power-feed)
    - [Controlling the Spindle](#controlling-the-spindle)
      - [Changing the Spindle Speed](#changing-the-spindle-speed)
      - [Starting the Spindle](#starting-the-spindle)
      - [Stopping the Spindle](#stopping-the-spindle)
      - [Resetting Spindle Speed to Default](#resetting-spindle-speed-to-default)
    - [Setting Offsets](#setting-offsets)
    - [Controlling Coolant/Lubrication](#controlling-coolantlubrication)
      - [Toggle Mist](#toggle-mist)
      - [Toggle Flood](#toggle-flood)
  - [Auto Mode](#auto-mode)
    - [Controlling Program Operations](#controlling-program-operations)
      - [Start a Loaded Program (Cycle Start)](#start-a-loaded-program-cycle-start)
      - [Step Through a Loaded Program (Single Block)](#step-through-a-loaded-program-single-block)
      - [Pause \& Resume a Running Program](#pause--resume-a-running-program)
      - [Stop a Running Program](#stop-a-running-program)
    - [Controlling Feed \& Rapid Overrides](#controlling-feed--rapid-overrides)
      - [Override Feed Percent](#override-feed-percent)
      - [Override Rapid Percent](#override-rapid-percent)
      - [Reset to Programmed Feed/Rapid Speeds](#reset-to-programmed-feedrapid-speeds)
    - [Controlling Spindle Overrides](#controlling-spindle-overrides)
      - [Override Spindle Percent](#override-spindle-percent)
      - [Reset Spindle Override](#reset-spindle-override)
    - [Controlling Coolant/Lubrication](#controlling-coolantlubrication-1)
  - [MDI Mode](#mdi-mode)
    - [Controlling Feed, Rapid and Spindle Overrides](#controlling-feed-rapid-and-spindle-overrides)
    - [Controlling Coolant/Lubrication](#controlling-coolantlubrication-2)
- [Installation](#installation)
  - [PlatformIO Install](#platformio-install)
  - [LinuxCNC Install](#linuxcnc-install)
- [Ini File Parameters](#ini-file-parameters)
  - [Standard Ini Parameters](#standard-ini-parameters)
    - [Section `[DISPLAY]`](#section-display)
    - [Section `[SPINDLE_0]`](#section-spindle_0)
    - [Section `[TRAJ]`](#section-traj)
  - [Manualmatic Ini Parameters](#manualmatic-ini-parameters)
    - [Section `[MANUALMATIC]`](#section-manualmatic)

<hr/>

# Operations

## Controls Overview

Manualmatic Pendant

<hr/>

## Display Overview

[Image: Annotated Screen]

## Machine On/Off, Abort Operation and Estop 

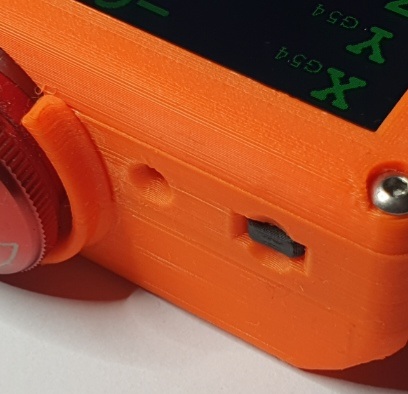
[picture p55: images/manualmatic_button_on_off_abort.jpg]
Manualmatic Button On/Off/Abort


The button on the top left of the Manualmatic is used to turn the machine on, off or abort a currently running operation. 

**Note:** This is the LinuxCNC definition of 'Machine On'.

### Turning On

If the machine is currently 'Off', a single press will turn the machine on.

### Turning Off 

If the machine is currently 'On' a long press will turn the machine off.
When the machine is 'off' the Manualmatic will display an on/off button:

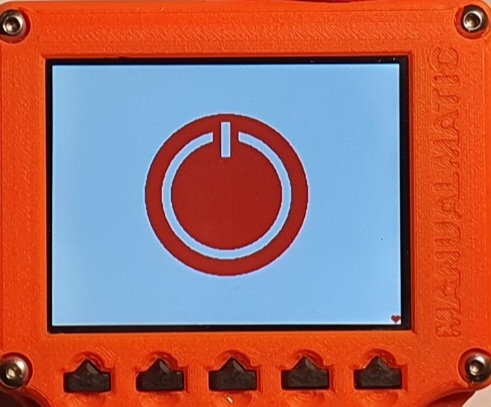
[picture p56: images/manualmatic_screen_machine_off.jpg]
Manualmatic screen off


Note: The machine cannot be started via button on the screen to prevent unintentional operation. 

### Abort Operation

In Manual mode, a short press will issue an 'abort' to the currently running operation. This can be useful if your machine is slow to catch up with an overly enthusiastic jog command.

In Auto mode, a short press will effectively issue a stop command to the currently running program.

### Soft Estop

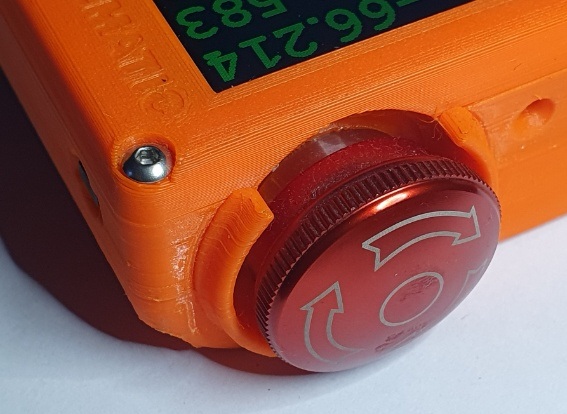
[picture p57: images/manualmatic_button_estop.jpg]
Manualmatic estop button


On the top right of the Manualmatic is the Soft Estop button. Press this to trigger LinuxCNC's Estop. Twist to release the estop.

**Please note:** this is a *soft* estop – ie runs through the Manualmatic via USB to the LinuxCNC userspace. It complements but must not be used as a substitute for the hard wired estop that you really (*really*) should also have present on your machine.

When the machine is estopped, the Manualmatic will display the halted icon:

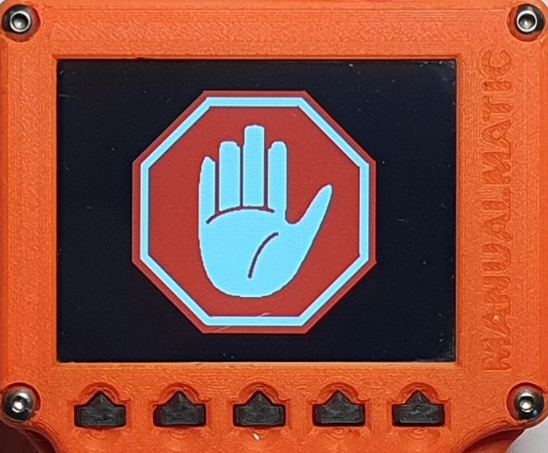
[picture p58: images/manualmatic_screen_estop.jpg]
Manualmatic estopped screen


<hr/>

## Operating Modes (Manual, MDI, Auto)

Just like the standard LinuxCNC GUIs, the Manualmatic operates in one of three modes: 

- Manual - use the Manualmatic to operate the mill almost as if it were a manual milling machine, prepare stock, set offsets in preparation for running CAM programs and control mist & flood.
- Auto - control the stop, start, pause and step of a loaded CAM program, view and override feed, rapid and spindle speeds of a running program and control mist & flood. 
- MDI - the Machine Data Interface for running short, manually entered G code.  The Manualmatic is currently for display purposes only in MDI mode.

### Changing Modes

The button on the right side of the Manualmatic will cycle through the normal modes for a CNC machine: Manual, Auto and MDI.

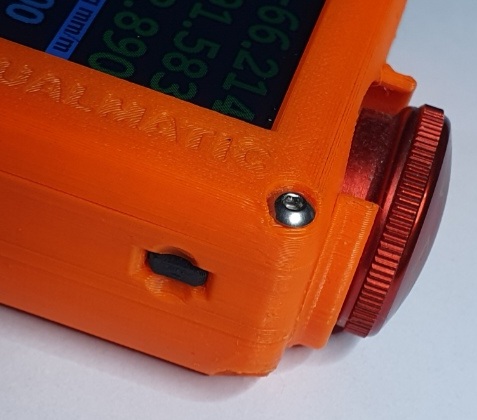
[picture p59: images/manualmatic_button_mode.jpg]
Manualmatic Mode Button


<hr/>

## Manual Mode

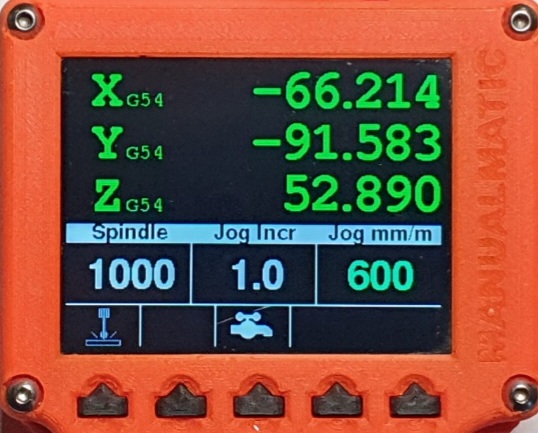
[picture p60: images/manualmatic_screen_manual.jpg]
Manualmatic Screen Manual Mode


### Controlling Jog/Feed Speeds & Increment

Note: In this section 'jog' and 'feed' are used to describe the same thing: moving the axis of the machine. 'Jog' is a term usually used for setting up and 'feed' for when actually cutting stock.

In LinuxCNC, manual jog speed and increments are *per input device*. All other information displayed on the Manualmatic will be syncronised with your main GUI but jog speed and increments used on the Manualmatic will not be reflected on the GUI and vice versa. 

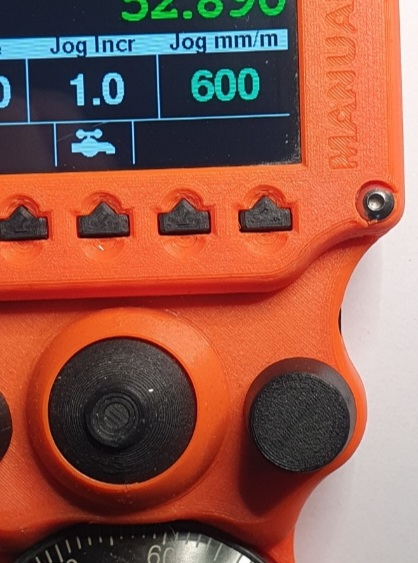
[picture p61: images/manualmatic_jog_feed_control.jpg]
Manualmatic Jog Control


#### Changing the Jog/Feed Speed

Turn the jog/feed control to increase or decrease the jog speed. The control has acceleration enabled, so if you spin the control faster, the jog rate will increment in bigger steps.

#### Changing Jog Increments

To change the Jog Increment, press and turn the jog/feed control.

#### Switching between Tortoise & Rabbit Range

Just like most of the LinuxCNC GUIs, there are two jog ranges, often called 'Tortoise' (for low jog/feed speed) and 'Rabbit' (the default, for fast speed).

A single press on the jog/feed control will toggle between the high and low ranges. 

#### Resetting Jog Speeds to Defaults

To reset to the default jog ranges, long press the jog/feed control. 
This will reset both Rabbit (100%) and Tortoise (10%) ranges. 

### Moving the Axis (Jogging)

#### Using the MPG

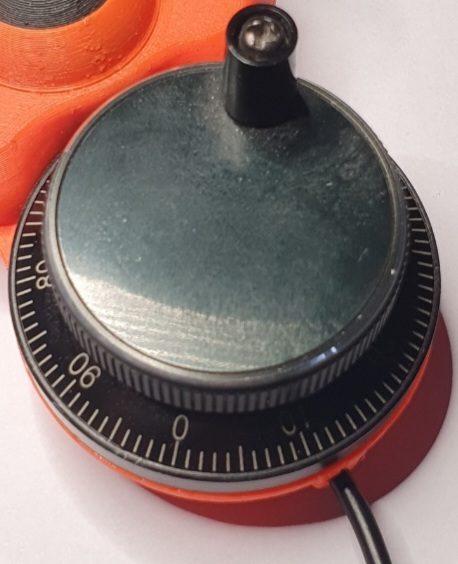
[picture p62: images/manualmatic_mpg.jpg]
Manualmatic MPG


The MPG (Manual Pulse Generator) is the traditional way to move an axis. Each 'click' of the control will move the selected axis by the selected jog increment.

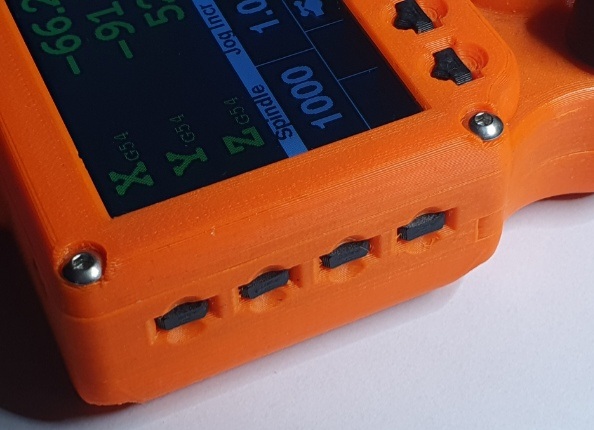
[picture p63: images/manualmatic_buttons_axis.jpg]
Manualmatic MPG


Select the required axis using the axis selector buttons on the left side of the Manualmatic, then turn the MPG to move the axis the required distance.
The selected axis will be indicated with a white arrow:

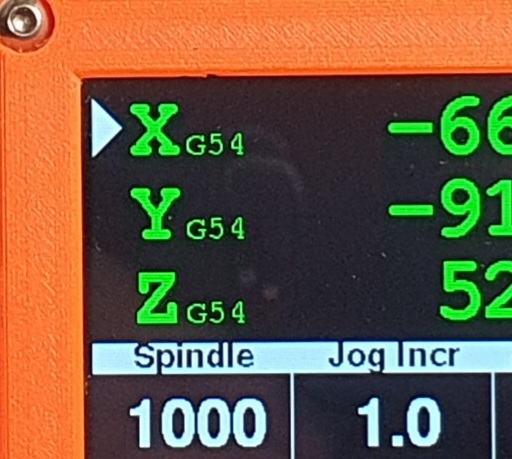
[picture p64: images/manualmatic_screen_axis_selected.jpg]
Manualmatic Selected Axis


#### Using the Joystick

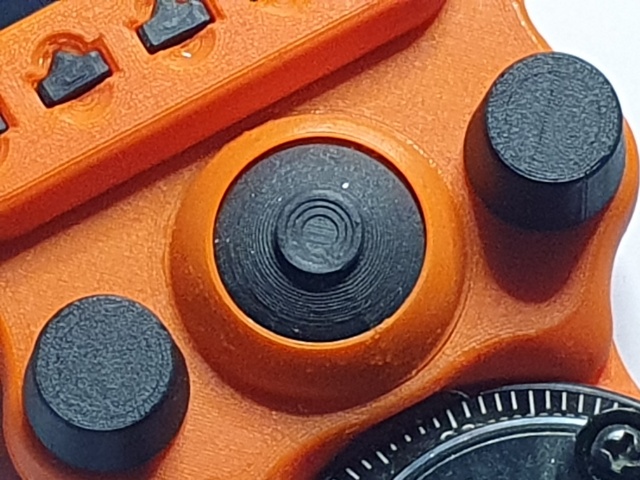
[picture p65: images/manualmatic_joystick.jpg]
Manaualmatic Joystick


The joystick can be used to rapidly move two axis. The speed and direction is controlled by the movement of the joystick, up to the displayed jog/feed rate. Note: the joystick is analog, so the jog increment does not apply.

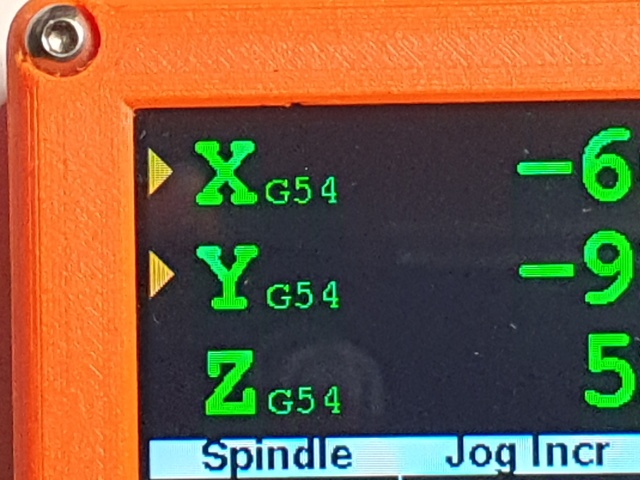
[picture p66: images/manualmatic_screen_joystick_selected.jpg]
Manualamatic Joystick Selected


By default, when one axis is moving, the other axis is 'locked' until the joystick is returned to centre. This is to improve the safety of power feed operations but if you want to move diagonally (or in circles) this can be overridden by holding down the modifier button when moving the joystick.

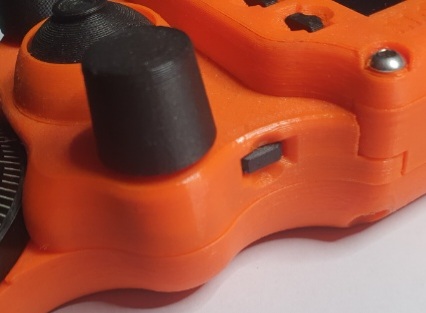
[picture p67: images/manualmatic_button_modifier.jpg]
Manualmatic Modifier Button


[Image: Circle trace]

#### Power Feed

The Joystick can be used in combination with the MPG for efficiently preparing stock. An axis can have both joystick and MPG enable or your can (for example) have the joystick enabled for X/Y and the MPG enabled for Z. This is very effective for facing operations.

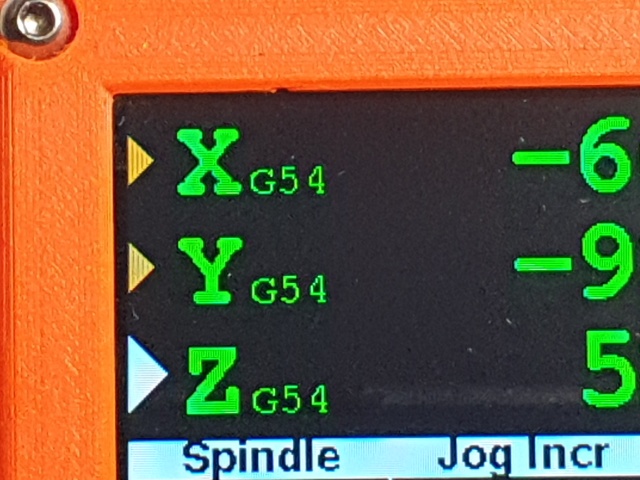
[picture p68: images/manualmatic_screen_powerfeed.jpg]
Manualmatic Powerfeed


### Controlling the Spindle

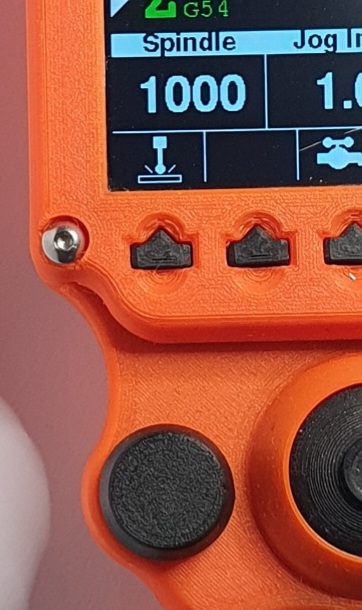
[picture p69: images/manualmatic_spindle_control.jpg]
Manualmatic Spindle Control


#### Changing the Spindle Speed

Turn the spindle control to increase or decrease the spindle speed.

The spindle speed can be changed before starting the spindle or while the spindle is running and will be incremented by one of the values set in the ini file as follows (in order of priority):

1. `[MANUALMATIC] SPINDLE_INCREMENT` You can also set this value to a set RPM (eg 100) or a percent (eg either 0.02 or 2%) for logarithmic-like behaviour. The percentage will be applied to the current spindle speed unless that value is less than 1 RPM.

2. `[DISPLAY] SPINDLE_INCREMENT` Also used by your GUI. 

3. `[SPINDLE_0] INCREMENT` I believe this is [incorrectly documented](https://github.com/LinuxCNC/linuxcnc/issues/3171#issuecomment-2453517563) as the `[SPINDLE_0]` section is intended to contain values for motion controller, not the display but is included here for completeness. 

The spindle control has acceleration enabled, so if you spin the control faster, the spindle speed will increment in larger steps.

The maximum spindle speed that can be set by the Manualmatic will be the lowest value of the following ini entries:

- `[SPINDLE_0] MAX_FORWARD_VELOCITY`
- `[SPINDLE_0] MAX_VELOCITY`
- `[DISPLAY] MAX_SPINDLE_0_SPEED`
- `[DISPLAY] MAX_SPINDLE_SPEED`

**Caution:** It may be possible to overspeed the spindle with the main GUI spindle override control (this is true even when the Manualmatic is not used).

The default spindle speed is set by the `[DISPLAY] DEFAULT_SPINDLE_SPEED` in your ini file.

[Image: Display spindle running]

When the spindle is running, the actual* RPM will be displayed below the requested RPM.

\* The 'actual' RPM is, by default, the spindle speed *requested* by LinuxCNC (RPM + override) read from the HAL pin `spindle.0.speed-out` but if you have a spindle encoder, you can specify a different HAL pin (must be RPM, not RPS) in the ini file `[MANUALMATIC] SPINDLE_RPM_PIN`.  

#### Starting the Spindle

To start the spindle, single press the spindle control and the choose 'Confirm' or 'Cancel'.
[Image: Display spindle confirm & cancel]

#### Stopping the Spindle

To stop the spindle, single press the spindle control and choose 'Confirm' or 'Cancel'.
[Image: Display spindle confirm & cancel]

#### Resetting Spindle Speed to Default

In Manual mode, a long press on the spindle control will reset the spindle override to 100% and if the spindle is not running, will reset the spindle speed to the default defined as `[DISPLAY] DEFAULT_SPINDLE_SPEED` in your `.ini` file.

### Setting Offsets

[Image: Offset Button]

When an axis is selected, the offset button will be enabled. Press the button or tap the screen to show the offset input keypad.

[Image: Display Offset keypad]

### Controlling Coolant/Lubrication

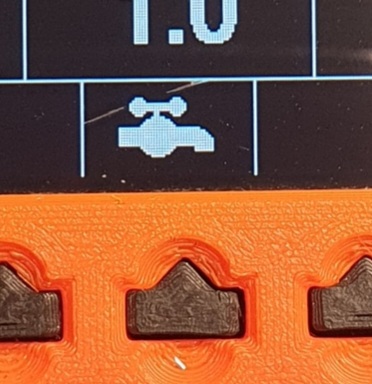
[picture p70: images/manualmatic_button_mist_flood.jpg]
Manualmatic Mist/Flood Button


#### Toggle Mist

To toggle mist on or off, single press the Mist/Flood Button or touch the screen icon.

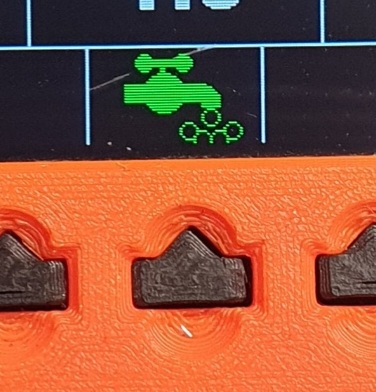
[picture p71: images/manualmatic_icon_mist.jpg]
Manualmatic Mist Icon


#### Toggle Flood

To toggle flood on or off, double press the Mist/Flood Button. The touch screen icon is not available for this function as there is not yet any 'double touch' function.

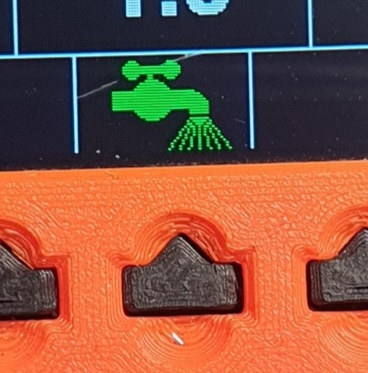
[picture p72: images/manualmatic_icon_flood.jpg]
Manualmatic Mist Icon


Note: It is possible to have both mist and flood operating at the same time.

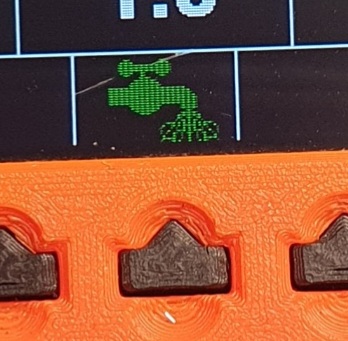
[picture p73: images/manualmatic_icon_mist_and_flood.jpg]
Manualmatic Mist Icon


<hr/>

## Auto Mode
In Auto mode the Manualmatic display will show real time axis coordinates, real time feed, rapid & spindle speeds and override percenatges.

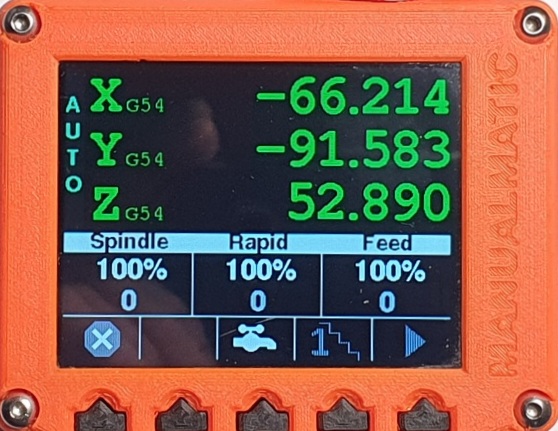
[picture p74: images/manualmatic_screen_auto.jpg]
Manualmatic Auto Mode


### Controlling Program Operations

The Manualmatic can control the running of a loaded CAM program. When a program is loaded, the buttons turn from grey (inactive) to green. 

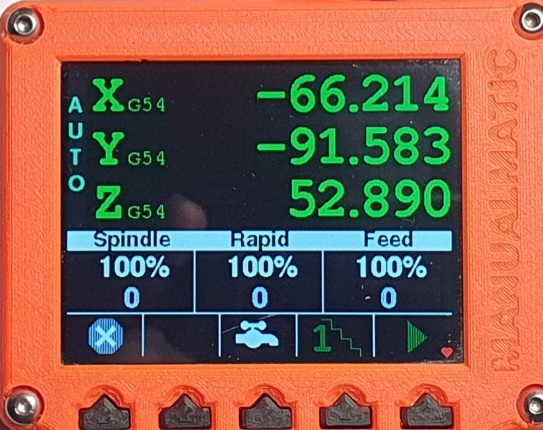
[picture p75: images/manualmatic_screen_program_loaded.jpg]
Manualmatic Auto Mode


#### Start a Loaded Program (Cycle Start)
To start a loaded program, press the 'Start' (Play) or the 'Step' button. 
To prevent accidental starting when pressing the Play button, you will be asked to confirm or cancel the requested action.
**Caution:** Currently the 'Step' button does not ask for confirmation, but this may change in the future (for first press only).
[Image: Cycle Start confirm/cancel buttons] 

#### Step Through a Loaded Program (Single Block)
To step through a new or paused CAM program, press the 'Step' icon. 
**Caution:** the Step will be started immediately without a confirmation prompt.
Please be sure you understand LinuxCNC's concept of a 'step' - it may not behave as you expect it. [This](https://forum.linuxcnc.org/38-general-linuxcnc-questions/43980-stepping-a-program-bug-or-feature?start=0) is a good thread on the subject. 
While a step is running, you can pause the program and then choose to continue stepping or fully resume.

#### Pause & Resume a Running Program
[Image: Cycle Resume/Step buttons]
[Image: Cycle Resume confirm/cancel buttons]
To pause a running program, press the 'Pause' button. The program will be paused immediatelly (ie without a confirm/cancel prompt).

To Resume a paused program, press the 'Resume' or 'Step' button. Consistent with starting a program 'Resume' will ask for confirmation but 'Step' will resume immediately.

**Note:** Pause does not stop the spindle, only the axis.

#### Stop a Running Program
To stop a running program, press the 'Stop' button (or the 'Abort' button on the top of the Manualmatic). 
The program will stop immediately, without a confirmation prompt.
[Image: Stop Program button]

### Controlling Feed & Rapid Overrides
[Image: Feed Override dial]
[Image: Display feed & rapid override]
#### Override Feed Percent

Turn the jog/feed control to increase or decrease the feed override percent. The control has acceleration enabled, so if you spin the control faster, the percentage will increment in bigger steps.

#### Override Rapid Percent

Press and turn the jog/feed control to increase or decrease the rapid override percent. Although control has acceleration enabled, it is not so easy to achieve when pressing the control!

#### Reset to Programmed Feed/Rapid Speeds
Press and hold the jog/feed control to reset both feed & rapid override to 100 percent.

### Controlling Spindle Overrides
[Image: Spindle override dial]
[Image: Display spindle override]

#### Override Spindle Percent
Turn the spindle control to increase or decrease the spindle override percent. The control has acceleration enabled, so if you spin the control faster, the percentage will increment in bigger steps.

#### Reset Spindle Override
Press and hold the jog/feed control to reset spindle override to 100 percent.

### Controlling Coolant/Lubrication
As per [Manual](#manual-mode) mode, both [Mist](#toggle-mist) and [Flood](#toggle-flood) coolant can be controlled via the Manualmatic.

<hr/>

## MDI Mode
### Controlling Feed, Rapid and Spindle Overrides
As per [Auto](#auto-mode) mode, [Feed](#adjust-feed-percent), [Rapid](#adjust-rapid-percent) and [Spindle](#adjust-spindle-percent) speed overrides can be controlled by the Manualmatic.

The spindle can also be started and stopped.

### Controlling Coolant/Lubrication
As per both [Manual](#manual-mode) and [Auto](#auto-mode) modes, both [Mist](#toggle-mist) and [Flood](#toggle-flood) coolant can be controlled via the Manualmatic.

<hr/>

# Installation

Clone or download [this repository](https://github.com/Stutchbury/Manualmatic-Pendant) and extract somewhere convenient (not usually on your LinuxCNC machine).

## PlatformIO Install

Use PlatformIO to install the firmware for the Manualmatic on to the Teensy 4.1.

- Follow the install instructions here: https://platformio.org/platformio-ide

- There are two folders of interest: 
  - The main codebase for the pendant: `Software/PlatformIO/pendant/ManualmaticPendant` or
  - A wiring check 'sketch': `Software/PlatformIO/pendant/ManualmaticWiringCheck` This only really required for PCB development or to check your soldering!

- Required libraries will be automatically downloaded based on the `platformio.ini` file.

Open either of these folders and PlatformIO will allow you to compile and upload.

## LinuxCNC Install

- Copy both `Manualmatic.py` (the class def) and `manualmatic` (the component, lowercase, no file extension) to your LinuxCNC config directory.
- Add the following line to custom.hal (replace `gmoccapy.ini` with your ini file name):    
`loadusr -W ./manualmatic gmoccapy.ini`
- Change the `manualmatic` file to executable. e.g. `chmod +x manualmatic` 
- Plug your manualmatic pendant into a USB port - make sure appears as `/dev/ttyACM0`
- Start LinuxCNC, preferably from the command line (to see any errors).

Note: LinuxCNC >= v2.9 now uses python3 with no default to 'python', so the `manualmatic` component file and the `mock_cnc_machine.py` file have been updated to use python3.

<hr/>

# Ini File Parameters

Ini file parameters are used to set default values and preferences on the Manualmatic.

## Standard Ini Parameters

These are the 'standard' options from your `.ini` file that are read by the Manualmatic Python component. Some may or may not exist as different config tools and/or GUIs create different parameters.

### Section `[DISPLAY]`

- `MAX_FEED_OVERRIDE`

- `MIN_SPINDLE_OVERRIDE`

- `MIN_SPINDLE_0_OVERRIDE`

- `MAX_SPINDLE_OVERRIDE`

- `MAX_SPINDLE_0_OVERRIDE`

- `DEFAULT_SPINDLE_SPEED`

- `DEFAULT_SPINDLE_0_SPEED`

- `MAX_SPINDLE_SPEED`

- `MAX_SPINDLE_0_SPEED`

- `DEFAULT_LINEAR_VELOCITY` For jogging.

- `MAX_LINEAR_VELOCITY`

### Section `[SPINDLE_0]`

- `MAX_FORWRD_VELOCITY`
- `MAX_VELOCITY`
- `INCREMENT`

### Section `[TRAJ]`

- `LINEAR_UNITS`

- `ANGULAR_UNITS`
  Not currently used.

- `DEFAULT_LINEAR_VELOCITY`

- `MAX_LINEAR_VELOCITY`

- `NO_FORCE_HOMING`
  Default: 0
  Do not force homing before jogging is allowed.

## Manualmatic Ini Parameters

### Section `[MANUALMATIC]`

This section defines options that are specific to the Manualmatic. These normally take precedence over options set elsewhere in the `ini` file.

- `SPINDLE_INCREMENT` This option can be set as RPM (eg 100) or a percent (eg either 0.02 or 2%) for logarithmic-like behaviour. The percentage will be applied to the current spindle speed unless that value is less than 1 RPM.
- `SPINDLE_RPM_PIN` The name of the hal pin that reports your spindle speed in RPM (not RPS). If not specified, the Manualmatic will use `spindle.0.speed-out` which is the RPM that LinuxCNC is requesting, not the actual RPM of the spindle.

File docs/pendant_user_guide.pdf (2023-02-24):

## Manualmatic CNCMPG/Pendant

## User Guide

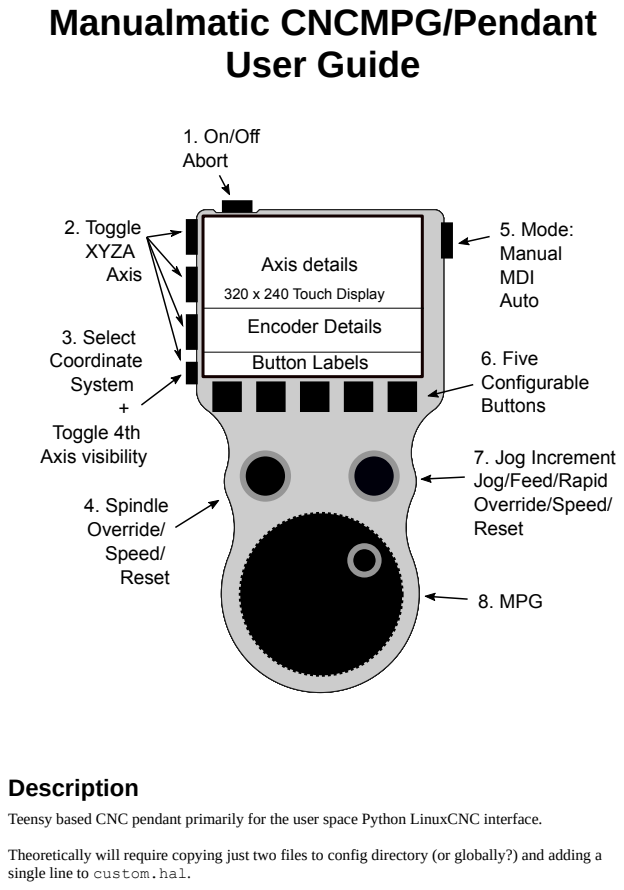
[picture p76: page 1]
Description; 1. On/Off; Abort; 2. Toggle; XYZA; Axis; 3. Select; Coordinate; System; Toggle 4th; Axis visibility; 5. Mode:; Manual; MDI; Auto; 6. Five; Configurable; Buttons; 4. Spindle; Override/; Speed/; Reset; 8. MPG; Axis details; Encoder Details; Button Labels; 320 x 240 Touch Display

7. Jog Increment
Jog/Feed/Rapid
Override/Speed/

Teensy based CNC pendant primarily for the user space Python LinuxCNC interface.

Theoretically will require copying just two files to config directory (or globally?) and adding a
single line to custom.hal.

Table of Contents

@TODO: Rewrite required. This document was written to provide development guidance and currently just describes the functions of each control rather than describing how to perform specific tasks.

Operation

Machine State

Most controls are inactive unless machine is on and homed.

On/off button is active at all times.

Spindle and feed knobs have acceleration enabled – if you turn the encoder fast it will increment in with larger values.

Many ini values are now read from the specified ini file to better match the GUI.

@TODO – work out how to do homing sequence via the Python interface (or MDI) – especially when number of joints != number of axis.

Mode: Manual

Control the CNC in manual mode – set offsets and perform manual machining, including spindle control.

### 1. On/Off Button

Click to turn machine on.

Long press to turn machine off.

When machine is on, click to send an Abort command (eg to stop a slow jog)

### 2. Axis Selectors

Toggle selection of axis X, Y, Z & A.

Deselecting an axis will also send a ‘jog stop’ command.

3. ‘A’ Button (Coordinate System)

Click to toggle selection of A axis if displayed

Double click to toggle between display of Abs and G5x coordinate system

Triple click to display DTG

Long press to toggle visibility of 4th axis

### 4. Spindle Encoder

Turn to set spindle RPM directly - once spindle is running, this control changes to override %

Double click to arm spindle - click button 5 to confirm start spindle or button 1 to cancel (click or double click of spindle encoder will also cancel)

Click to stop spindle – button 5 to confirm spindle stop, button 1 to cancel (ie spindle will keep running)

Long press to reset spindle override and (if not running) pendant to default spindle speed

### 5. Mode Button

Switch mode to MDI or Auto.

### 6. Configurable Buttons

## 1. Set G5x offset for selected axis

Only active when an axis is selected.

## 2. ~Half selected axis

Not yet implemented (may add to offset screen instead)

## 3. Toggle Coolant

Click to toggle coolant/mist. Double click to toggle flood.

### 7. Feed Encoder

Rotate to change jog velocity

Press+rotate to change jog increments

Click to toggle between high and low range jog velocity

Long press to reset to default jog velocity

### 8. MPG Encoder

Jog selected axis

### 9. Joystick

Click to arm primary axes (default is X/Y). Double click to arm secondary axes (default is Z). These axis are set in ManualmaticConfig.h.

Move in the desired direction – max jog velocity is determined by the value set by the feed encoder above. There are 8 increments between min and max velocity (this can be changed in ManualmaticConfig.h but may be read from an ini setting in the future).

Mode: Auto

Control the CNC machine in auto mode. Start, stop, pause and single step a loaded program. Adjust feed, rapid and spindle rates.

### 1. On/Off Button

Click to turn machine on.

Long press to turn machine off.

When machine is on, click will send Abort command.

### 2. Axis Selectors

Not enabled in auto mode.

3. ‘A’ Button (Coordinate System)

Double click to toggle between display of Abs and G5x coordinate system

Triple click to display DTG

Long press to toggle visibility of 4th axis

### 4. Spindle Speed/Override

Turn to adjust spindle override

Long press to reset spindle override

### 5. Mode Button

Switch mode to Manual or MDI only when program is not loaded or stopped

### 6. Configurable Buttons

## 1. Halt running program

Active when program is running, paused or single stepping.

## 3. Toggle Coolant

As per manual mode.

## 4. Single step through program

Active when program has not yet started or is paused, single step through program.

## 5. Run/Pause Program

Active/displayed when program is not loaded, paused or in single step, press to start running the program.

Active/displayed when program is running (or while a single step is not yet complete) to pause the program.

### 7. Feed Encoder

Rotate to adjust feed override

Press+Rotate to adjust rapid override

Long press to reset to default feed/rapid velocity

Mode: MDI

Not currently implemented. This will likely become the ‘conversational’ part of the pendant if that need arises.

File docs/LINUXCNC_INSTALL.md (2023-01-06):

### LinuxCNC Install

One of the goals of this project was a 'plug-n-play' pendant and although it's not quite that, it is very easy to install into LinuxCNC - no hal pin configuration required.

## 1. Copy Two Files

Copy both ```Manualmatic.py``` (a Python class definition) and ```manualmatic``` (the LinuxCNC component, lowercase, no file extension) to your LinuxCNC config directory. 

Set the execute permission on the ```manualmatic``` file. (Right-click on the file in File Manager, choose the 'Permissions' tab)

## 2. Update ```custom.hal``` File

Add the following line to ```custom.hal``` (replace ```gmoccapy.ini``` with your ```ini``` file name or you *will* get an error - ask me how I know):    

```loadusr -W ./manualmatic gmoccapy.ini```

The ```custom.hal``` file will normally already exist but it may not for the example sim configurations.

If the ```custom.hal``` file does not exist, create it and add the line above and then in your configuration's ```.ini``` file (```gmocappy.ini``` in this example) add the following line: 

```HALFILE = custom.hal``` 

to the ```[HAL]``` section.

## 3. Plug in Your Manualmatic

Plug your manualmatic pendant into a USB port - make sure appears as ```/dev/ttyACM0``` (from a terminal type: ```ls -l /dev/ttyACM0```)

This port can be changed in the ```manualmatic``` file but ```ttyACM0``` is the default port for a Teensy.

## 4. Start LinuxCNC

Start LinuxCNC normally. Sometimes it takes a little while for the component to load after plugging in the USB for the first time.

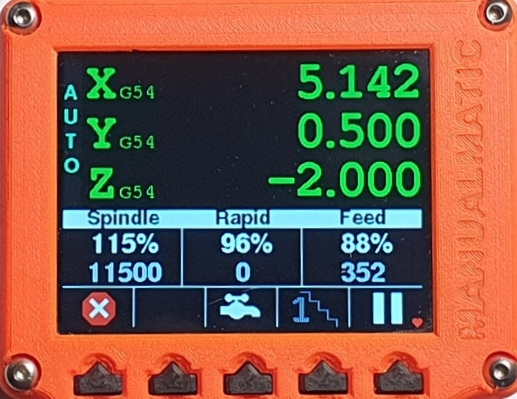
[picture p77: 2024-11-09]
images/manualmatic_screen_feed_spindle_overrides.jpg

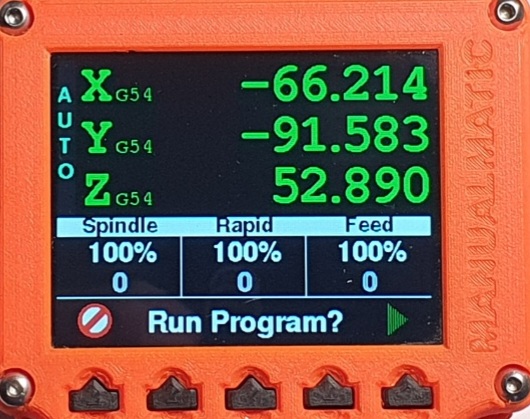
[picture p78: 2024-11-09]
images/manualmatic_screen_confirm_program_run.jpg

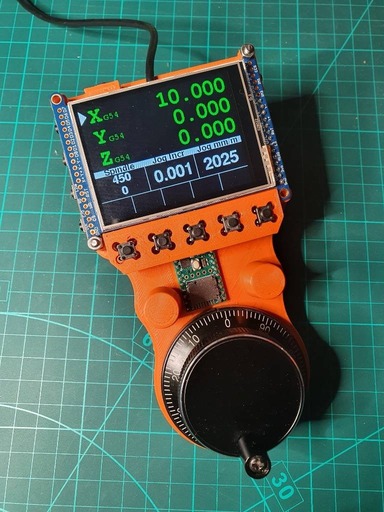
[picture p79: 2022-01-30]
images/manualmatic-pendant_2021-12-30.jpeg

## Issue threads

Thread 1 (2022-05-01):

TFT in SPI mode

jam-sys, 2022-05-01:
First of all: Thanks for your excellent project.

I have a question.
In your schematic, you connect IM1, IM2 and IM3 pins to GND.
The Adafruit documentation recommend to tie these pins to 3.3 Volts.
What is the proper way?

Stutchbury, 2022-05-01:
> First of all: Thanks for your excellent project.

Thank you.

>
> I have a question. In your schematic, you connect IM1, IM2 and IM3 pins to GND. The Adafruit documentation recommend to tie these pins to 3.3 Volts. What is the proper way?

It took me a little while to work this one out as I'd not knowingly referenced IM1-3!

In the schematic, pins 15-18 on J1 are actually connections to the corner pads of the display/PCB for a modified symbol (and footprint) that provides pads only for the connections required by the Manualmatic. If I'd used the Adafruit footprint, it would have placed down both sides leaving no room for buttons.

The IM1, IM2 and IM3 SPI Mode Jumpers (on the back of the display) are closed with solder as per the Adafruit instructions here: https://learn.adafruit.com/adafruit-2-8-and-3-2-color-tft-touchscreen-breakout-v2/spi-wiring-and-test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

I have updated the schematic with a comment which will hopefully help.

Closed 2022-05-04.

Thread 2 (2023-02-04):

Option to compile for STM32?

TadyTheFish, 2023-02-04:
Hello!
Love the project you have made and I would like to make it for my machine, but I would like to know if it is possible to compile it for a STM32F1 or F4 MCU? I have a bunch laying around and no Teensy and they are not really so cheap as STMs
I tried to compile for STM but it seems that the min, max and round macros are not defined in STM32 core .. Go figure. And the compiler throws a lot of errors ManualmaticControl.cpp and ManualMAticDisplay.cpp, Something about no suitable conversion function from "lambda []
Maybe it is because a different compiler is used for the STM32. I know how to code stuff but lambdas are out of my scope :)
Thank you

Stutchbury, 2023-02-06:
Hi Tady - the Manualmatic is kinda designed around the Teensy 4.1 - primarily for the number of pins, speed of processor and PJRC's interrupt driven encoder library. I have never compiled any code for STM32, so unfortunately am not best placed to advise you. I suspect the missing macros and lambdas are part of the included Arduino or Teensy libraries?

TadyTheFish, 2023-02-06:
Yeah PJRC's enoder library is portes for more platforms. Those missing macros are a strange thing if you ask me min, max andround should be a part of the core...
The biggest problem for me is those lambda errors.
Whell no problem thank you for your time and this great project. I will mark this as closed 😁

Closed 2023-02-06.

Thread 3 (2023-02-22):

linuxcnc not starting

TadyTheFish, 2023-02-22:
I'm having a problem with you project. I cant start Linuxcnc
I followed your instructions
- Added both files to the root of my config directory
- added `loadusr -W ./manualmatic gmoccapy.ini `to core_sim.hal (I use gmoccapy.ini for my config file)
- started linuxcnc with `linuxcnc gmoccapy.ini`
It throws an error:
```
LINUXCNC - 2.10.0~pre0
Machine configuration directory is '/home/linuxcnc/Desktop/tady'
Machine configuration file is 'gmoccapy.ini'
Starting LinuxCNC...
linuxcnc TPMOD=tpmod HOMEMOD=homemod EMCMOT=motmod
Note: Using POSIX realtime
Found file(REL): ./core_sim.hal
./core_sim.hal:10: execv(./manualmatic): No such file or directory
./core_sim.hal:10: waitpid failed ./manualmatic manualmatic
./core_sim.hal:10: ./manualmatic exited without becoming ready
Shutting down and cleaning up LinuxCNC...
HostMot2 ethernet driver unloaded
Note: Using POSIX realtime
LinuxCNC terminated with an error.  You can find more information in the log:
    /home/linuxcnc/linuxcnc_debug.txt
and
    /home/linuxcnc/linuxcnc_print.txt
as well as in the output of the shell command 'dmesg' and in the terminal
```
The files are where they should be. I changed the /dev/ttyS0 to /dev/ttyACM0 in manualmatic
I'm out of ideas. I use the dev run in place
Thank you

TadyTheFish, 2023-02-22:
I changed the shebang in manualmatic from `#!/usr/bin/python` to `#!/usr/bin/python3` and it loads up but threre are other problems
```
Traceback (most recent call last):
  File "/home/linuxcnc/Desktop/tady/./manualmatic", line 28, in <module>
    mm.connect(PORT)
  File "/home/linuxcnc/Desktop/tady/Manualmatic.py", line 714, in connect
    self.sendIniValues()
  File "/home/linuxcnc/Desktop/tady/Manualmatic.py", line 196, in sendIniValues
    self.writeToSerial(self.CMD_INI_VALUE+self.INI_AXES, format(self.ls.axes))
AttributeError: 'linuxcnc.stat' object has no attribute 'axes'. Did you mean: 'axis'?
```
If i change to axis there is a tuple error

TadyTheFish, 2023-02-22:
here is an explanation
https://forum.linuxcnc.org/29-forum-announcements/47328-master-is-now-linuxcnc-v2-10
it's actually 2.9 . So it seems I'm a little to far ahead :)
Thanks for the links I know a little about linuxcnc and I modified a mesa ethernet driver for a STM32 board, but I don't know alot more of the internals. So I will dig a little trough the docs and source to modify your code :)

TadyTheFish, 2023-02-22:
wll Try to modify it :D

Stutchbury, 2023-02-22:
The code shouldn't be too hard (after all, I wrote it! :) ) - please leave notes here - I'll leave this ticket open.

TadyTheFish, 2023-02-23:
Don't sell your self short. Your coding skills ar wayyy batter than mine but I will try my best 😁

TadyTheFish, 2023-02-23:
Well there seems to be a problem with Linuxcnc 2.9 (2.10). I added `print(dir(linuxcnc.stat))` to manualmatic (component file) and it printed out:
`['__class__', '__delattr__', '__dir__', '__doc__', '__eq__', '__format__', '__ge__', '__getattribute__', '__gt__', '__hash__', '__init__', '__init_subclass__', '__le__', '__lt__', '__ne__', '__new__', '__reduce__', '__reduce_ex__', '__repr__', '__setattr__', '__sizeof__', '__str__', '__subclasshook__', 'acceleration', 'active_queue', 'actual_position', 'adaptive_feed_enabled', 'ain', 'angular_units', 'aout', 'axis', 'axis_mask', 'block_delete', 'call_level', 'command', 'current_line', 'current_vel', 'cycle_time', 'debug', 'delay_left', 'din', 'distance_to_go', 'dout', 'dtg', 'echo_serial_number', 'enabled', 'estop', 'exec_state', 'feed_hold_enabled', 'feed_override_enabled', 'feedrate', 'file', 'flood', 'g5x_index', 'g5x_offset', 'g92_offset', 'gcodes', 'homed', 'ini_filename', 'inpos', 'input_timeout', 'interp_state', 'interpreter_errcode', 'joint', 'joint_actual_position', 'joint_position', 'joints', 'kinematics_type', 'limit', 'linear_units', 'lube', 'lube_level', 'max_acceleration', 'max_velocity', 'mcodes', 'misc_error', 'mist', 'motion_id', 'motion_line', 'motion_mode', 'motion_type', 'num_extrajoints', 'optional_stop', 'paused', 'pocket_prepped', 'poll', 'position', 'probe_tripped', 'probe_val', 'probed_position', 'probing', 'program_units', 'queue', 'queue_full', 'queued_mdi_commands', 'rapidrate', 'read_line', 'rotation_xy', 'settings', 'spindle', 'spindles', 'state', 'task_mode', 'task_paused', 'task_state', 'tool_from_pocket', 'tool_in_spindle', 'tool_offset', 'tool_table', 'velocity']`
No Axes .. to me it seems to be a Linuxcnc bug ... We should report this to the official forum

Stutchbury, 2023-02-23:
Well that's a bit worrying. If you could raise a ticket on the LinuxCNC repository that would be very much appreciated (I don't currently have a 2.9 or 2.10 install).
Perhaps also one for the poll() argument too - at least a documentation update.
I have tried (in the past too) to find out where the Python Interface is defined in src so I can understand it better but always end up down the wrong rabbit hole...

TadyTheFish, 2023-02-23:
I was also wondering where could I find this in the source code🤔. How do you open a ticket. I never did this?

Stutchbury, 2023-02-23:
Let me know if you find it! This is where you raise issues for LinuxCNC: https://github.com/LinuxCNC/linuxcnc/issues
When you click 'New issue' it provides a 'template' to ease you through the submission - the same process as this one but a much bigger, more talented & organised development community!

TadyTheFish, 2023-02-23:
I did some digging and I THINK these python things are here:
`/home/linuxcnc/linuxcnc-dev/src/emc/usr_intf/axis/extensions/emcmodule.cc`

andypugh, 2023-02-23:
The issue is the use of stat.axes to return the number of axes in use.

The code should now iterate through the axis mask instead. This is because previously you needed dummy axes for lathes or other configurations with a missing axis. So lathes (XZ) needed a dummy Y, and a 4 axis XYZC mill would need a dummy A and B.

See https://github.com/LinuxCNC/linuxcnc/commit/ffe664c0422887c899be5cd59de6b1cb1d1bbc4c

Stutchbury, 2023-02-23:
Well done - looking at the history of that file, it would seem axis and axes were deprecated in 2015! I didn't see mention of that in the Python Interface...

https://github.com/LinuxCNC/linuxcnc/commit/ffe664c0422887c899be5cd59de6b1cb1d1bbc4c

Stutchbury, 2023-02-23:
I've just noticed you discovered the same thing...

TadyTheFish, 2023-02-24:
I faked your python file and added 3 instead of self.ls.axes and it works, even with a Aliexpress LCD (when RESET pin is also connected).
I moved the `loadusr -W ./manualmatic gmoccapy.ini` to the gmoccapy_postgui.hal (that was also my mistake).
I also tested the axes_mask and it returns 7 on a XYZ machine. So the code needs some adjusting to take the mask value and turn it in to number of axes:)
Also I couldnt see the PDF file (that you posted on the linuxcnc forum) here on your git repo

andypugh, 2023-02-24:
I think this should be left open until there is a fix that works for all users, rather than one user putting in a workaround.

Stutchbury, 2023-02-24:
I have re-opened - I probably need to rework the use/checking of valid axes. The code is currently focused on a very simple 3 axis mill - I just needed to start making chips!

TadyTheFish, 2023-02-24:
I closed the issue thinking there is an answer to the problem.. Sorry

Stutchbury, 2023-02-24:
No worries. I have added the (more-dev-than-user) User Guide here: https://github.com/Stutchbury/Manualmatic-Pendant/blob/main/docs/pendant_user_guide.pdf

Stutchbury, 2023-02-24:
I have pushed a new version of Manualmatic.py ( https://github.com/Stutchbury/Manualmatic-Pendant/blob/main/Software/linuxcnc/python-component/Manualmatic.py ) that removes the use of the deprecated linuxcnc.stat.axes so should work for 2.8, 2.9 and 1.20.

This does raise questions on non-contiguous axes (eg XYZB rather than XYZA) but given that I've not written anything for rotational axes, that falls squarely in the todo/too hard pile.

If you could test on your 2.9 & 2.10 installs, that would be much appreciated.

TadyTheFish, 2023-02-27:
I will do some tests tomorow. I use teensy 3.6 with an aliexpress LCD.
I do have two other thing to advise.
1. Change `#!/usr/bin/python` in manualmatic component file to `#!/usr/bin/python3`
Or make a note in the documentation (readme) for people to install `$ sudo apt install python-is-python3`
2. Make a note in the documentation (readme) for people to install pySerial. It's the only dependency
`pip3 install pySerial` or `pip install pySerial`

Way easier for people that struggle with programming stuff 😉

Stutchbury, 2023-02-27:
Thanks. I've not tested with a Teensy 3.6 so I'll be interested to know if it works. I tried python3 on my 2.8 install last week and it couldn't find the hal component, so I probably need to do a bit more research.
I've never had to install pySerial on 2.8 (I've just done a fresh install on a NUC without having to) but I'll make a note in the docs. Perhaps a difference between Python 2 and 3?

TadyTheFish, 2023-02-27:
Some quick testing showed me that it does work with 3.6 and maybe even 3.5. Nothing to change just compile for 3.6.
The lcd works and it connects to linuxcnc. My MPG didn't work. I selected the X axis and when i turned the MPG nothing happened 🤷‍♂️ i will test some more maybe there is a kink in my MPG.
As for your python3 problem i had the reverse problem. With 2.9 (2.10) if I leave everything as is, linuxcnc does not find the manualmatic file, but if I change the shebang to python3 it works

TadyTheFish, 2023-02-27:
Maybe it's best to leave the shebang and make a note "if you use linuxcnc 2.9 and newer install python-is-python3"

Stutchbury, 2023-02-27:
I will definitely make notes in the docs. Can I suggest you use 2.8 to test your pendant - too many variables if you're also using a Teensy 3.6!

TadyTheFish, 2023-02-27:
I need to reinstall the whole system for 2.8. I have a spare disk I can use. What do you mean by too many variables? how do you debug the component? HAL does not show any signals or pins?

Stutchbury, 2023-02-27:
The 'too many variables' is that you're using a Teensy 3.6 and a a possibly dodgy MPG with LinuxCNC 2.9+ - I have tested against 2.8 so you can be sure that will work in order to test the Teensy 3.6 and your MPG. Once you're sure they're working as expected then move to testing 2.9+ with a known working pendant.
Hal will not show any pins for the component because we are using the user space Python interface. The easiest way to debug the component is to run LinuxCNC from the command line - if you right click on the desktop icon for your config and choose the 'Properties' and then 'Desktop Entry' it will show the command you need to run.
For my Pi the sim config is: `/usr/bin/linuxcnc '/home/pi/linuxcnc/configs/sim.gmoccapy/gmoccapy.ini'` - yours will be something similar.
Any `print()` commands you put in the Python code will be echoed to the terminal.

TadyTheFish, 2023-02-27:
I run my instance in a terminal (I use the RIP enviroment). Aaaa ok that is what I wanted to know if you debug with print() or is there a option to do it in HAL. Glad that is cleared up :)
Ok I will install 2.8 on a disk and test with that

Stutchbury, 2023-07-06:
I have now tested on 2.9  using the buildbot debs for Debian 12 (and even have dual boot Buster/2.8 & Bookworm/2.9 on my mill).
The only issue is that vanilla 2.9 requires `#!/usr/bin/python3` hash bang in the `manualmatic` component file rather than just `#!/usr/bin/python`.
The latest code for Manualmatic is currently in the dev branch - will push when I'm happy it is all stable.

TadyTheFish, 2023-07-06:
We slould probably close this issue. I have put on hold this project since I'm currently developing an EtherCAT to analog servo interface. But I will come back for this :)

Closed 2023-07-06.

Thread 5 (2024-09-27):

PCB schematic

ulope, 2024-09-27:
Our makerspace is just building its MPCNC and I discovered this project - really awesome, thanks for making it open!

I was wondering if you plan to release the PCB schematic (and ideally, component bom, production files, etc.) as well?

Stutchbury, 2024-09-28:
Hi Ulrich
It was always the plan to release the PCB files but I wanted to get it into the hands of other people before I did. And now I've updated laptop/KiCAD which has slightly broken my design (I had custom footprints that haven't quite come across properly).
In the meantime, I have a few spare PCBs and thank to Mouser minimum order value) usually a few of the components - my email is in my github profile.

Closed 2024-12-21.

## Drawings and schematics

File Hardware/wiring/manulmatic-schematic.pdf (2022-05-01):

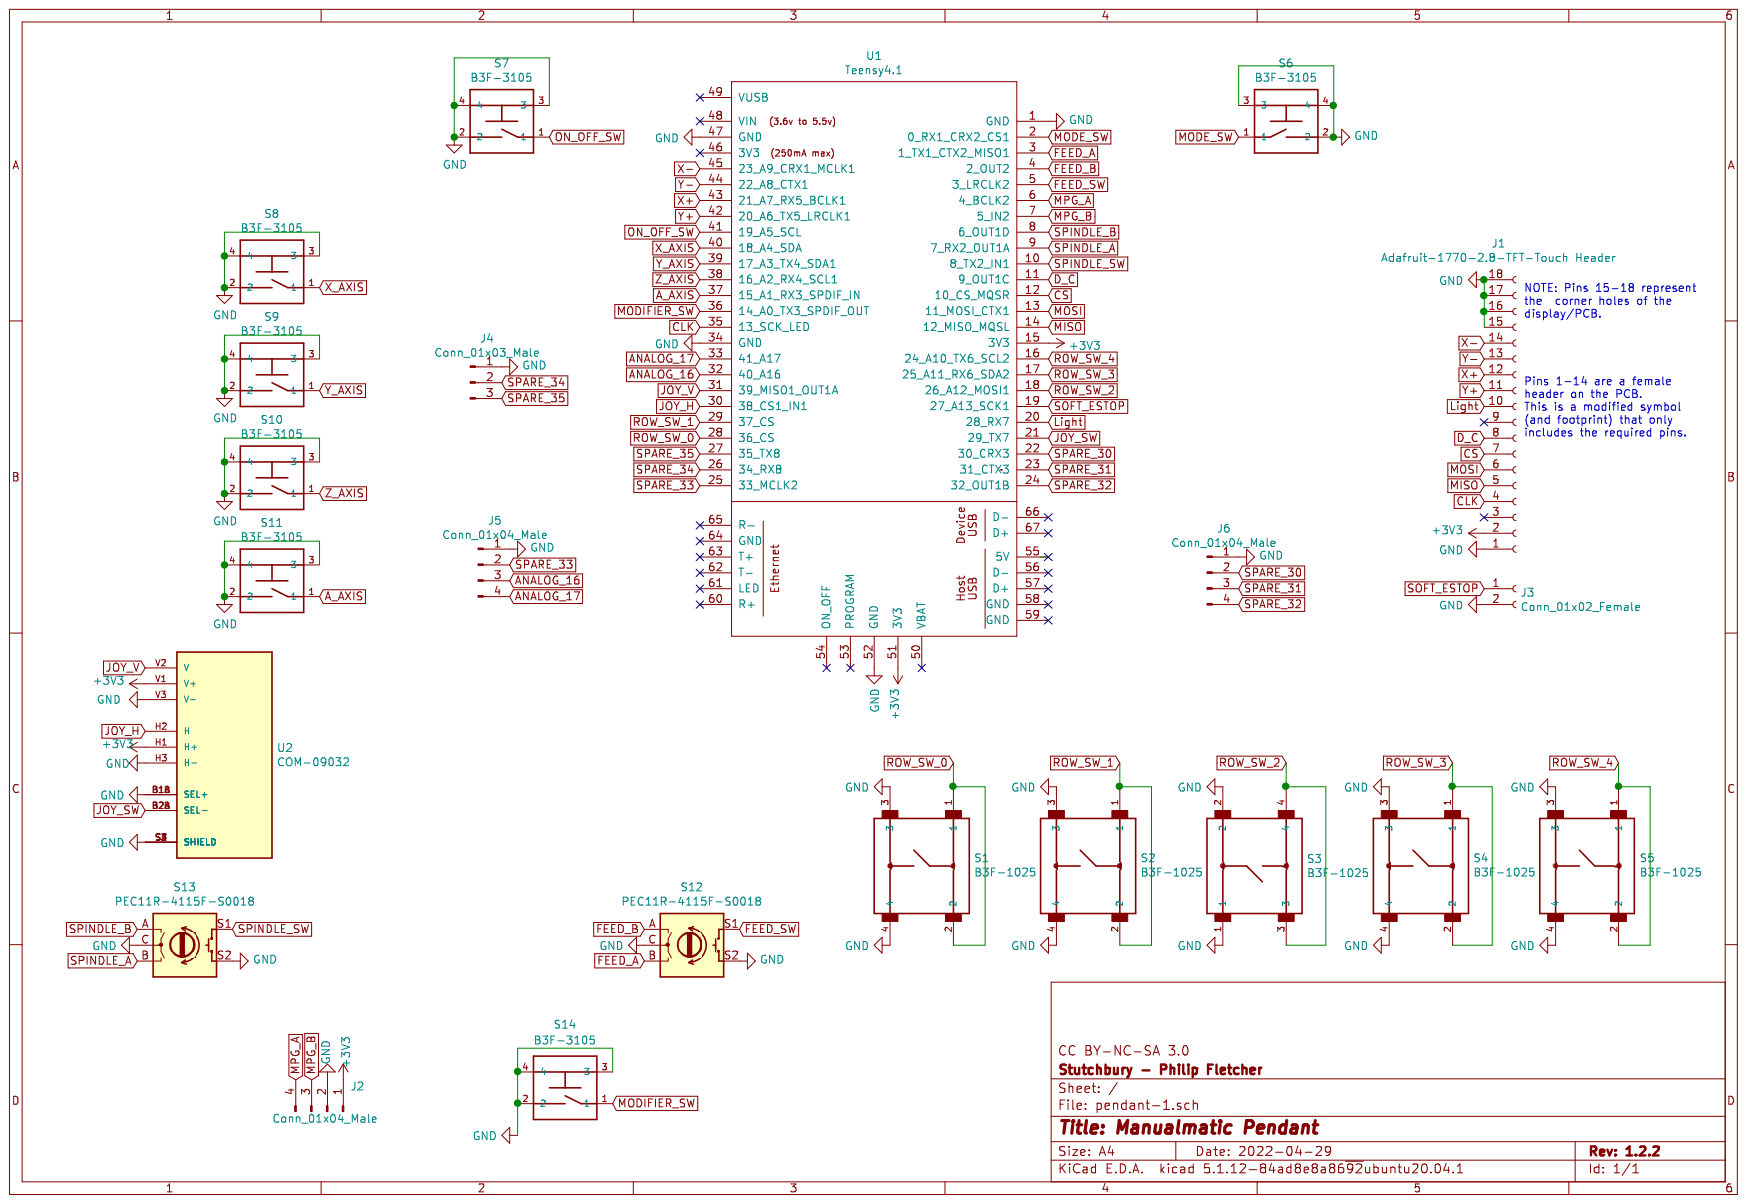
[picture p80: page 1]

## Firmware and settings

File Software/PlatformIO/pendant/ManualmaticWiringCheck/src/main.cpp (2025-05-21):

/** 
 * 
 * Manualmatic Pendant Wiring Check
 * 
 * Test the display, touchscreen, buttons, encoders and joystick 
 * on the pendant are all present and correctly wired.
 * 
 * Copy the contents of ManualmaticWiring.h from the main project.
 * 
 * GPLv2 Licence https://www.gnu.org/licenses/old-licenses/gpl-2.0.txt
 * 
 * Copyright (c) 2022 Philip Fletcher <philip.fletcher@stutchbury.com>
 * 
 */


#include <Arduino.h>
#include <Adafruit_GFX.h>
#include <Adafruit_ILI9341.h>
#include <TouchScreen.h>
#include <EventButton.h>
#include <EncoderButton.h>
#include <EventJoystick.h>
#include "ManualmaticWiring.h"

// Use hardware SPI (on Uno, #13, #12, #11) and the above for CS/DC
Adafruit_ILI9341 gfx = Adafruit_ILI9341(TFT_CS, TFT_DC);

TouchScreen ts = TouchScreen(TOUCHSCREEN_XP, TOUCHSCREEN_YP, TOUCHSCREEN_XM, TOUCHSCREEN_YM, TOUCHSCREEN_OHMS);
unsigned long lastTsUpdate = millis();
unsigned long heartbeatUpdate = millis();

//Encoders
EncoderButton feed(ENCODER_A_FEED, ENCODER_B_FEED, BUTTON_FEED);
EncoderButton mpg(ENCODER_A_MPG, ENCODER_B_MPG);
EncoderButton spindle(ENCODER_A_SPINDLE, ENCODER_B_SPINDLE, BUTTON_SPINDLE);
// //Buttons
EventButton buttonOnOff(BUTTON_ON_OFF);
EventButton buttonX(BUTTON_X);
EventButton buttonY(BUTTON_Y);
EventButton buttonZ(BUTTON_Z);
EventButton buttonA(BUTTON_A);
EventButton buttonMode(BUTTON_MODE);
EventButton buttonModifier(BUTTON_MODIFIER);
EventButton buttonRow[5] = { 
  EventButton(BUTTON_ROW_0), 
  EventButton(BUTTON_ROW_1), 
  EventButton(BUTTON_ROW_2), 
  EventButton(BUTTON_ROW_3),
  EventButton(BUTTON_ROW_4)
};
//Joystick
EventJoystick joystick(JOYSTICK_X, JOYSTICK_Y);
EventButton buttonJoystick(BUTTON_JOYSTICK);
void clr() {
  gfx.fillRect(0,200, 320, 40, 0);
  Serial.println();
  heartbeatUpdate = millis();
}
void onFeedEncoder(EncoderButton& btn) { 
  clr(); 
  gfx.printf("Feed encoder: %i \n", btn.position());
  Serial.printf("Feed encoder: %i \n", btn.position());
}
void onSpindleEncoder(EncoderButton& btn) { 
  clr(); 
  gfx.printf("Spindle encoder: %i \n", btn.position()); 
  Serial.printf("Spindle encoder: %i \n", btn.position()); 
}
void onMpgEncoder(EncoderButton& btn) { 
  clr(); 
  gfx.printf("MPG encoder: %i \n", btn.position()); 
  Serial.printf("MPG encoder: %i \n", btn.position()); 
}
void onFeed(EncoderButton& btn) { 
  clr(); 
  gfx.println("Feed button"); 
  Serial.println("Feed button"); 
}
void onSpindle(EncoderButton& btn) { 
  clr(); 
  gfx.println("Spindle button"); 
  Serial.println("Spindle button"); 
}
void onOnOff(EventButton& btn) { 
  clr(); 
  gfx.println("On/Off button"); 
  Serial.println("On/Off button"); 
}
void onX(EventButton& btn) { 
  clr(); 
  gfx.println("X axis button"); 
  Serial.println("X axis button"); 
}
void onY(EventButton& btn) { 
  clr(); 
  gfx.println("Y axis button"); 
  Serial.println("Y axis button"); 
}
void onZ(EventButton& btn) { 
  clr(); 
  gfx.println("Z axis button"); 
  Serial.println("Z axis button"); 
}
void onA(EventButton& btn) { 
  clr(); 
  gfx.println("A axis button"); 
  Serial.println("A axis button"); 
}
void onMode(EventButton& btn) { 
  clr(); 
  gfx.println("Mode button"); 
  Serial.println("Mode button"); 
}
void onRow(EventButton& btn) { 
  clr(); 
  gfx.printf("Row button %i \n", btn.userId()); 
  Serial.printf("Row button %i \n", btn.userId()); 
}
void onModifier(EventButton& btn) { 
  clr(); 
  gfx.println("Modifier button"); 
  Serial.println("Modifier button"); 
}
void onJoystick(EventButton& btn) { 
  clr(); 
  gfx.println("Joystick button"); 
  Serial.println("Joystick button"); 
}
void onJoystickMoved(EventJoystick& ej) {
  clr(); 
  gfx.printf("Joystick X: %i, Y: %i \n", ej.x.position(), ej.y.position());
  Serial.printf("Joystick X: %i, Y: %i \n", ej.x.position(), ej.y.position());
}



void setup() {
  // put your setup code here, to run once:
  Serial.begin(115200);
  delay(200);
  Serial.println("Hello World");
  gfx.begin();
  gfx.setRotation(1);
  gfx.fillScreen(0);
  mpg.setEncoderHandler(onMpgEncoder);
  feed.setEncoderHandler(onFeedEncoder);
  spindle.setEncoderHandler(onSpindleEncoder);
  feed.setClickHandler(onFeed);
  spindle.setClickHandler(onSpindle);
  buttonOnOff.setClickHandler(onOnOff);
  buttonX.setClickHandler(onX);
  buttonY.setClickHandler(onY);
  buttonZ.setClickHandler(onZ);
  buttonA.setClickHandler(onA);
  buttonMode.setClickHandler(onMode);
  buttonModifier.setClickHandler(onModifier);
  for (uint8_t col=0; col<5; col++) {
    buttonRow[col].setClickHandler(onRow);
    buttonRow[col].setUserId(col);    
  }
  joystick.setChangedHandler(onJoystickMoved);
  buttonJoystick.setClickHandler(onJoystick);
  gfx.setTextSize(2);
  gfx.setCursor(5,50);
  gfx.println("Manualmatic Wiring Check:");
  gfx.setCursor(5,70);
  gfx.println("1. Press each button.");
  gfx.setCursor(5,90);
  gfx.println("2. Turn encoders");
  gfx.setCursor(5,110);
  gfx.println("3. Press encoders");
  gfx.setCursor(5,130);
  gfx.println("4. Touch screen");
}

void loop() {
  // put your main code here, to run repeatedly:
  gfx.setCursor(5,200);
  mpg.update();
  feed.update();
  spindle.update();
  buttonOnOff.update();
  buttonX.update();
  buttonY.update();
  buttonZ.update();
  buttonA.update();
  buttonMode.update();
  buttonModifier.update();
  for (uint8_t col=0; col<5; col++) {
    buttonRow[col].update();    
  }
  buttonJoystick.update();
  joystick.update();


  if ( millis() > lastTsUpdate + 100 ) {
    lastTsUpdate = millis();

  //   // a point object holds x y and z coordinates
    TSPoint p = ts.getPoint();
    
  //   // we have some minimum pressure we consider 'valid'
  //   // pressure of 0 means no pressing!
    if (p.z > ts.pressureThreshhold) {
      clr();
      gfx.printf("Touch X: %i, Y: %i \n", p.x, p.y);
      Serial.printf("Touch X: %i, Y: %i \n", p.x, p.y);
    }
  }

  if ( millis() > heartbeatUpdate + 1000 ) {
    heartbeatUpdate = millis();
    Serial.print(".");
  }
}

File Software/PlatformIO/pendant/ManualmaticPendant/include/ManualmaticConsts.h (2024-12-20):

/**
 * @file ManualmaticConsts.h
 * @author Philip Fletcher <philip.fletcher@stutchbury.com>
 * @brief Mostly enums but a fair few consts as well.
 * Where applicable, the enums map onto the values used in the LinuxCNC 
 * Python Interface.
 * All valid commands are defined here - the same mapping exists in the Python class.
 * @version 0.1
 * @date 2022-03-01
 * 
 * @copyright Copyright (c) 2022
 * GPLv2 Licence https://www.gnu.org/licenses/old-licenses/gpl-2.0.txt
 * 
 */


#ifndef ManualmaticConsts_h
#define ManualmaticConsts_h

#include <Arduino.h>

#define MANUALMATIC_RELEASE "v0.2.0"
// Color definitions @TODO Move to display?
//https://github.com/adafruit/Adafruit_ILI9341/blob/master/Adafruit_ILI9341.h
//https://chrishewett.com/blog/true-rgb565-colour-picker/
#define BLACK 0x0000       ///<   0,   0,   0
#define NAVY 0x000F        ///<   0,   0, 123
#define DARKGREEN 0x03E0   ///<   0, 125,   0
#define DARKCYAN 0x03EF    ///<   0, 125, 123
#define MAROON 0x7800      ///< 123,   0,   0
#define PURPLE 0x780F      ///< 123,   0, 123
#define OLIVE 0x7BE0       ///< 123, 125,   0
#define LIGHTGREY 0xC618   ///< 198, 195, 198
#define DARKGREY 0x7BEF    ///< 123, 125, 123
#define BLUE 0x001F        ///<   0,   0, 255
#define GREEN 0x07E0       ///<   0, 255,   0
#define CYAN 0x07FF        ///<   0, 255, 255
#define RED 0xF800         ///< 255,   0,   0
#define MAGENTA 0xF81F     ///< 255,   0, 255
#define YELLOW 0xFFE0      ///< 255, 255,   0
#define WHITE 0xFFFF       ///< 255, 255, 255
#define ORANGE 0xFD20      ///< 255, 165,   0
#define GREENYELLOW 0xAFE5 ///< 173, 255,  41
#define PINK 0xFC18        ///< 255, 130, 198
#define LIGHTGREEN 0x8fee  


/**
 * @brief Follows the convention of linuxcnc (except INIT)
 */
enum Task_state_e : uint8_t {
  STATE_INIT, STATE_ESTOP, STATE_ESTOP_RESET, STATE_OFF, STATE_ON
};

/**
 * @brief Follows the convention of linuxcnc (except UNKNOWN)
 */
enum Task_mode_e : uint8_t {
  MODE_UNKNOWN, MODE_MANUAL, MODE_AUTO, MODE_MDI
};

/**
 * @brief Follows the convention of linuxcnc
 */
enum Motion_type_e : uint8_t {
  MOTION_TYPE_NONE, MOTION_TYPE_TRAVERSE, MOTION_TYPE_FEED, MOTION_TYPE_ARC, MOTION_TYPE_TOOLCHANGE, MOTION_TYPE_PROBING, MOTION_TYPE_INDEXROTARY
};

/**
 * @brief Follows the convention of linuxcnc - except INTERP_UNKNOWN
 */
enum Interp_e : uint8_t {
  INTERP_UNKNOWN, INTERP_IDLE, INTERP_READING, INTERP_PAUSED, INTERP_WAITING
};

/**
 * @brief Follows the convention of linuxcnc
 */
enum Flood_e : uint8_t {
  FLOOD_OFF, FLOOD_ON
};

/**
 * @brief Follows the convention of linuxcnc
 */
enum Mist_e : uint8_t {
  MIST_OFF, MIST_ON
};


/**
 * @brief Follows the convention of linuxcnc
 */
enum AutoCmd_e : uint8_t {
  AUTO_RUN, AUTO_STEP, AUTO_PAUSE, AUTO_RESUME
};

/**
 * @brief Follows the convention of linuxcnc
 */
enum Exec_state_e : uint8_t {
  RCS_DONE, RCS_EXEC, RCS_ERROR
};

enum Display_coords_e : uint8_t {
  DISPLAY_COORDS_ABS, DISPLAY_COORDS_DTG, DISPLAY_COORDS_G5X, DISPLAY_COORDS_NONE, 
};

/**
 * @brief The state of a program when in 'auto' mode
 * 
 */
enum Program_state_e : uint8_t {
  PROGRAM_STATE_NONE, PROGRAM_STATE_RUNNING, PROGRAM_STATE_PAUSED, PROGRAM_STATE_STOPPED
};


enum Operation_e : uint8_t {
  OPERATION_NONE, OPERATION_POWERFEED
};


/**
 * @brief Initialisation state of the pendant
 */
enum Ini_state_e : uint8_t {
  INI_STATE_DISCONNECTED, INI_STATE_CONNECTED, INI_STATE_RECEIVED, INI_STATE_SENT
};


/**
 * @brief Valid values for cmd[0]
 * Do not use enum class
 */
enum Cmd_e : uint8_t {
  CMD_ABSOLUTE_POS = 'A', // Absolute position
  CMD_SPINDLE_SPEED = 'S', //Commanded spindle speed (not RPM unless override is 100%) IN/OUT
  CMD_SPINDLE_OVERRIDE = 's', //Spindle override - combined with speed results in RPM IN/OUT
  CMD_SPINDLE_RPM = 'R', //Actual RPM of spindle as a result of SPINDLE_SPEED * OVERRIDE IN
  CMD_SPINDLE_DIRECTION = 'G', //Spindle direction IN
  CMD_FEED_OVERRIDE = 'f', //Feed override IN/OUT
  CMD_RAPID_OVERRIDE = 'r', //Rapid override IN/OUT
  CMD_JOG = 'J', //Jog
  CMD_JOG_VELOCITY = 'j', //Jog Velocity IN/OUT (sorta)
  CMD_JOG_CONTINUOUS = 'N', //Jog continuous (Nudge) payload is velocity
  CMD_JOG_STOP = 'n', //Jog stop (don't nudge)
  CMD_TASK_MODE = 'M', //mode IN/OUT
  CMD_TASK_STATE = 'E', //task_state (Estop and On/Off) IN/OUT
  CMD_INTERP_STATE = 'I', //interp_state
  CMD_CURRENT_VEL = 'v', //current_vel
  CMD_MOTION_TYPE = 't', //motion_type
  CMD_G5X_INDEX = 'W', //g5x_index (WCS) IN OUT
  CMD_G5X_OFFSET = '5', //g5x_offset IN
  CMD_G92_OFFSET = '9', //g92_offset IN
  CMD_TOOL_OFFSET = 'T', //Tool_offset IN: offset OUT: tool index?
  CMD_DTG = 'D', //DTG
  CMD_ALL_HOMED = 'H', //homed
  CMD_HOMED = 'h', //homed
  CMD_INI_VALUE = 'i', //ini value
  CMD_FLOOD = 'C', //Coolant IN/OUT
  CMD_MIST = 'c', //Little Coolant IN/OUT
  CMD_EXEC_STATE = 'e', 
  CMD_PROGRAM_STATE = 'p',
  CMD_AUTO = 'a',
  CMD_HEARTBEAT = 'b' //Heartbeat
};
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

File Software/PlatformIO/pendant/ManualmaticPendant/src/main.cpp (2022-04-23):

/**
 * @file main.cpp
 * @author Philip Fletcher <philip.fletcher@stutchbury.com>
 * @brief Main file for Manualmatic Pendant
 * @version 0.0.1
 * @date 2022-02-25
 * 
 * @copyright Copyright (c) 2022
 * 
 * GPLv2 Licence https://www.gnu.org/licenses/old-licenses/gpl-2.0.txt
 * 
 */
#include <Arduino.h>

//We are dependent on GFX but not to a particular screen
#include "Adafruit_GFX.h"
#include "Adafruit_ILI9341.h"
#include "TouchScreen.h"

#include "Manualmatic.h"


// Use hardware SPI
Adafruit_ILI9341 gfx = Adafruit_ILI9341(TFT_CS, TFT_DC);

TouchScreen ts = TouchScreen(TOUCHSCREEN_XP, TOUCHSCREEN_YP, TOUCHSCREEN_XM, TOUCHSCREEN_YM, TOUCHSCREEN_OHMS);

Manualmatic manualmatic(Serial, gfx, ts);

void setup() {
  // put your setup code here, to run once:
  Serial.begin(115200);
  delay(200);

   gfx.begin();
   manualmatic.begin();

}

void loop() {
  // put your main code here, to run repeatedly:
  manualmatic.update();
}

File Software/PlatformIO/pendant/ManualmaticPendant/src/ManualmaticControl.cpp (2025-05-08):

#include "ManualmaticControl.h"


ManualmaticControl::ManualmaticControl(ManualmaticMessage& serialMessage, 
                                      ManualmaticConfig& config, 
                                      ManualmaticState& s, 
                                      ManualmaticButtonRowKeypad& brkp,
                                      ManualmaticOffsetKeypad& okp
                                      )
    : message(serialMessage),
      config(config),
      state(s),
      brkp(brkp),
      okp(okp),
      messenger(serialMessage, config, s), 
      feed(ENCODER_A_FEED, ENCODER_B_FEED, BUTTON_FEED),
      mpg(ENCODER_A_MPG, ENCODER_B_MPG),
      spindle(ENCODER_A_SPINDLE, ENCODER_B_SPINDLE, BUTTON_SPINDLE),
      buttonOnOff(BUTTON_ON_OFF),
      buttonX(BUTTON_X),
      buttonY(BUTTON_Y),
      buttonZ(BUTTON_Z),
      buttonA(BUTTON_A),
      buttonMode(BUTTON_MODE),
      buttonModifier(BUTTON_MODIFIER),
      rowButtons { 
        EventButton(BUTTON_ROW_0),
        EventButton(BUTTON_ROW_1),
        EventButton(BUTTON_ROW_2),
        EventButton(BUTTON_ROW_3),
        EventButton(BUTTON_ROW_4)
      },
      joystick(JOYSTICK_X, JOYSTICK_Y),
      buttonJoystick(BUTTON_JOYSTICK)
{ }
/** ********************************************************************** */
void ManualmaticControl::begin() {
  //pinMode(SOFT_ESTOP, INPUT_PULLUP);
  estopSwitch.attach(SOFT_ESTOP, INPUT_PULLUP);
  setupEncoders();
  setupButtons();
  setupButtonRowKeypad();
  setupOffsetKeypad();
  setupJoystick();
  checkEstop(true);
}
/** ********************************************************************** */
void ManualmaticControl::update() {
  checkEstop();
  state.now = millis();
  if ( state.iniState == INI_STATE_RECEIVED ) {
    onIniReceived();
  }
  char cmd[2];
  char payload[30];
  if ( message.available(cmd, payload)) {
    state.update(cmd, payload);
  }
  //Check if button row is different to state button row
  if (buttonRow != state.buttonRow) {
    setupButtonRow(state.buttonRow);
    buttonRow = state.buttonRow;
  }
  mpg.update();
  feed.update();
  spindle.update();
  buttonOnOff.update();
  buttonX.update();
  buttonY.update();
  buttonZ.update();
  buttonA.update();
  buttonMode.update();
  okp.update();  //Do draw() in updateDisplay()
  brkp.update(); //Ditto
  updateButtonRow();
  joystick.update();
  buttonJoystick.update();
  buttonModifier.update();

  checkHeartbeat();  

}
/** ********************************************************************** */
void ManualmaticControl::setupEncoders() {
  //Configure the encoders
  feed.setRateLimit(feedRateLimit);
  feed.setEncoderHandler([&](EncoderButton &eb) { onFeedEncoder(eb); } );
  feed.setEncoderPressedHandler([&](EncoderButton &eb) { onFeedPressedEncoder(eb); } );
  feed.setClickHandler([&](EncoderButton &eb) { onFeedClicked(eb); } );
  feed.setLongPressHandler([&](EncoderButton &eb) { onFeedLongPress(eb); } );

  spindle.setRateLimit(spindleRateLimit);
  spindle.setEncoderHandler([&](EncoderButton &eb) { onSpindleEncoder(eb); } );
  spindle.setClickHandler([&](EncoderButton &eb) { onSpindleClicked(eb); } );
  spindle.setTripleClickHandler([&](EncoderButton &eb) { onSpindleTripleClicked(eb); } );
  spindle.setLongPressHandler([&](EncoderButton &eb) { onSpindleLongPressed(eb); } );

  mpg.setRateLimit(mpgRateLimit);
  mpg.setEncoderHandler([&](EncoderButton &eb) { onMpgEncoder(eb); } );
}
/** ********************************************************************** */
void ManualmaticControl::setupButtons() {
  buttonOnOff.setClickHandler([&](EventButton &btn) { onOffClicked(btn); });
  buttonOnOff.setLongPressHandler([&](EventButton &btn) { onOnOffLongPress(btn); });
  buttonOnOff.setLongClickDuration(longClickDuration);

  buttonX.setClickHandler([&](EventButton &btn) { toggleXSelected(btn); });  
  buttonX.setLongClickDuration(longClickDuration);

  buttonY.setClickHandler([&](EventButton &btn) { toggleYSelected(btn); });  
  buttonY.setLongClickDuration(longClickDuration);
  
  buttonZ.setClickHandler([&](EventButton &btn) { toggleZSelected(btn); });  
  buttonZ.setLongClickDuration(longClickDuration);
  
  
  buttonA.setClickHandler([&](EventButton &btn) { toggleASelected(btn); });  
  buttonA.setDoubleClickHandler([&](EventButton &btn) { toggleDisplayAbsG5x(btn); });
  buttonA.setTripleClickHandler([&](EventButton &btn) { displayDtg(btn); });
  buttonA.setLongPressHandler([&](EventButton &btn) { onButtonALongPressed(btn); });
  buttonA.setLongClickDuration(longClickDuration);
  
  buttonMode.setClickHandler([&](EventButton &btn) { onButtonModeClicked(btn); });
  buttonMode.setLongClickDuration(longClickDuration);

  for ( uint8_t b=0; b<5; b++ ) {
    rowButtons[b].setUserId(BUTTON_NONE);
    rowButtons[b].setLongClickDuration(longClickDuration);
    //Set all buttons in button row to same handler
    rowButtons[b].setClickHandler([&](EventButton &btn) { onButtonRowButtonClicked(btn); });
    rowButtons[b].setDoubleClickHandler([&](EventButton &btn) { onButtonRowDoubleClicked(btn); });
  }

  buttonModifier.setPressedHandler([&](EventButton &btn) { onButtonModifierPressed(btn); });
  buttonModifier.setReleasedHandler([&](EventButton &btn) { onButtonModifierReleased(btn); });


}

void ManualmaticControl::setupButtonRowKeypad() {
  brkp.enable(false);
  for (uint8_t col=0; col<5; col++) {
    brkp.key(0,col).setTouchedHandler([&](TouchKey &key) { onButtonRowTouched(key); });
    //Draw handlers are set in ManualmaticDisplay
  }
}


void ManualmaticControl::setupOffsetKeypad() {
  okp.enable(false); 
  okp.key(3,0).setTouchedHandler([&](TouchKey &key) { onTouchCancelG5xOffset(key); });
  okp.key(3,4).setTouchedHandler([&](TouchKey &key) { onTouchSetG5xOffset(key); });
  //Draw handlers are set in ManualmaticDisplay
}

void ManualmaticControl::setupJoystick() {
  joystick.setRateLimit(config.joystickRateLimit);
  joystick.x.setStartBoundary(config.joystickStartBoundary);
  joystick.y.setStartBoundary(config.joystickStartBoundary);
  joystick.x.setEndBoundary(config.joystickEndBoundary);
  joystick.y.setEndBoundary(config.joystickEndBoundary);
  joystick.setNumIncrements(config.numJoystickIncrements);
  joystick.x.setChangedHandler([&](EventAnalog &js) { onJoystickXChanged(js); });
  joystick.y.setChangedHandler([&](EventAnalog &js) { onJoystickYChanged(js); });
  joystick.setIdleHandler([&](EventJoystick &js) { onJoystickIdle(js); });
  //Disable the joystick but allow callibration (everyone plays with the joystick!)
  joystick.enable(false, true);
  buttonJoystick.setClickHandler([&](EventButton &btn) { onJoystickClicked(btn); });
  buttonJoystick.setDoubleClickHandler([&](EventButton &btn) { onJoystickDoubleClicked(btn); });
}
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

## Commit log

2022-01-24 Add proof of concept 3D models.
    [pendant-test2-PartBody_base.stl, pendant-test2-PartBody_keypad1.stl]
2022-01-27 Add schematic and Arduino sketch to check encoder and button wiring
2022-01-28 Add knob for prototype cradle
    [knob-PartBody16mm.stl]
2022-01-29 Add the linuxcnc manualmatic component and a mock linuxcnc machine
    [mock.ini]
2022-01-29 Add the Arduino manualmatic sketch
2022-01-31 Added temporary bezel stl
    [bezel-Part.stl]
2022-02-03 Rename overloaded function to work with EncoderButton update.
2022-02-24 PlatformIO build for Wiring Check
2022-02-26 Updated schematic
2022-02-26 Point README to PlatformIO wiring check
2022-02-26 Remove Arduino wiring check sketch
2022-04-23 Updated wiring check for PCB v1.1
2022-04-23 Initial migration of pendant code from Arduino IDE to PlatformIO
2022-04-23 Case for v1.1
    [button-panel-left.stl, button-panel-right.stl, cable-wedge.stl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]
2022-04-23 Case image
2022-04-25 Larger relief for non-square encoders
    [encoder-panel.stl]
2022-04-25 Remove Arduino sketch
2022-04-29 Update row buttons to correct mfr part number
2022-05-01 Clarify custom display symbol on schematic
2022-05-13 Initial draft of Bill of Materials
2022-05-13 Fix BOM table layout?
2022-05-14 Move BOM to docs folder
2022-05-15 Add soldering guide
2022-05-15 Image alignment for soldering doc
2022-06-27 Add button STLs
    [cable-grip-2-wire.stl, row-button.stl, side-button.stl]
2022-06-27 Add row button cube
    [row-button-cube.stl]
2022-09-29 Test STEP export of case
    [base-Part.step]
2023-04-02 Set spindle override correctly
    [Manualmatic.py]
2023-04-30 Correct the name of the manualmatic estop hal pin.
2023-05-20 Hot plug fixes.
    * Fix heartbeat handling on reconnection
    * Stop jogging on disconnection
    * Disable serial debug output by default and improve output format
    [Manualmatic.py]
2023-05-22 Implement transient error message display.
    [ManualmaticConsts.h, ManualmaticControl.cpp, ManualmaticDisplay.cpp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]
2023-05-25 Add spindle handling to mock
    [mock.ini]
2023-05-25 Make spindle control more intuitive
2023-05-25 Fix error if [SPINDLE_0]MAX_VELOCITY does not exist in ini file
    [Manualmatic.py]
2023-07-13 Set max spindle speed to 24,000rpm if max not defined in .ini file
2023-07-19 Display current G5x
2023-07-19 Display current G5x (the correct py file!)
    [Manualmatic.py]
2023-07-19 Handle program error more gracefully
    [Manualmatic.py]
2023-09-05 Prevent joystick click unless centred
    [ManualmaticControl.cpp]
2023-10-15 Add pictures of fully soldered PCB
2023-10-15 Update BOM, add all components to table
2023-10-15 BOM additions/corrections
2023-10-15 Add stand-offs to BOM
2024-02-24 Fix error when turning machine on from pendant.
    [Manualmatic.py]
2024-03-03 Make power feed safer - multi-axis joystick moves now require modifier button to be pressed.
2024-03-05 Add cradle model to hold the Manualmatic on a vertical surce
    [cradle.stl]
2024-10-24 Add triple click to reverse displayed spindle RPM
    [ManualmaticControl.cpp]
2024-10-24 Ensure spindle is not running when toggling displayed direction!
2024-11-04 Use qtvcp logger instead of print()
2024-11-17 Major update to spindle control
2024-12-08 Prevent startup failure if no spindle defined in ini file
    [Manualmatic.py]
2025-05-08 Mode button toggle only Manual and Auto (not MDI)
2025-05-21 Add Serial output and heartbeat for wiring check without a display
